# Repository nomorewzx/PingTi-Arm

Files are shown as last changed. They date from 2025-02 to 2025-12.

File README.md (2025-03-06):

# PingTi Arm - A Low-Cost Robotic Arm with Human Arm Length 🤖💪

<center> <a href=./docs/README_CN.md> 中文版 </a> </center>

## What is PingTi Arm? 🤔

**PingTi Arm** is an open-source robotic arm designed based on the [SO-100 arm](https://github.com/TheRobotStudio/SO-ARM100) and is compatible with [Lerobot](https://github.com/huggingface/lerobot). The name "PingTi" comes from the Chinese pinyin "平替" (píng tì), which means "affordable substitute"

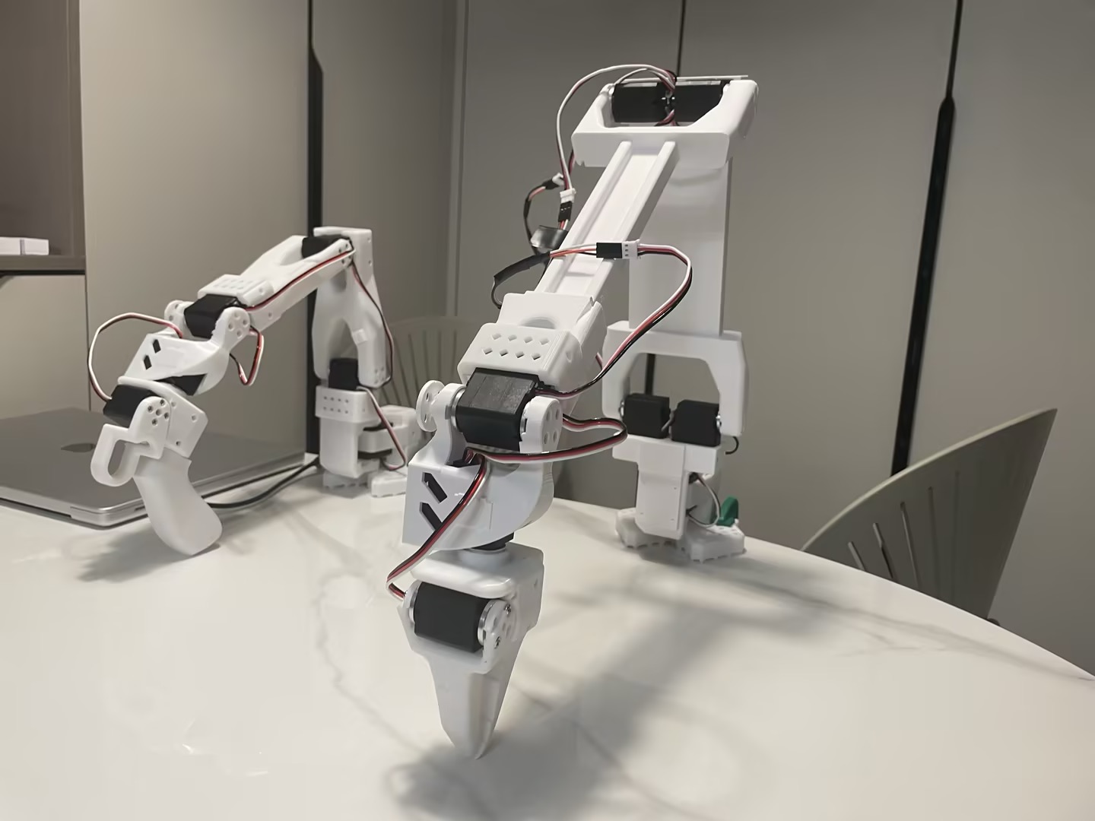
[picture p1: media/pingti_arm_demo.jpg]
PingTi Arm


## Features 
- **Human arm scale**: 600mm arm span (excluding the end effector).
- **Reasonable payload**: Supports up to 500g at maximum arm span.
- **Support setting up Leader-Follower arms** you can setup a pair of Leader-Follower arm using PingTi Arm as follower arm and SO-100 as leader arm
- **Compatible with Lerobot**, You can run teleoperation, data collection and other tasks that Lerobot supports via [pingti_lerobot_bridge](https://github.com/nomorewzx/pingti_lerobot_bridge) sdk
- **Cost Effective**: 
  - A single PingTi arm costs ~ USD 261, 
  - A Lead-Follower setup costs ~ USD 390.
  - If you already own an SO-100 follower arm (12V, 30kg.cm servos), you only need 2 additional servos and a USB drive board (~$157) to assemble the PingTi arm.

## Docs
- [Bills of Materials List](./docs/BOM_List.md) ｜ [Bills of Materials List 中文版](./docs/BOM_List_CN.md)
- [3D Printing](./docs/3d_print.md)
- [Assembly tutorial](./docs/Assembe_tutorial.md)
- [Example of run teleoperation and other tasks via `pingti_lerobot_bridge`](https://github.com/nomorewzx/pingti_lerobot_bridge)
- **(TODO)**: PingTi Arm on [LeKiwi base](https://github.com/SIGRobotics-UIUC/LeKiwi)
- **(TODO)**: [URDF for Simulation](./docs/URDF_SIM.md)

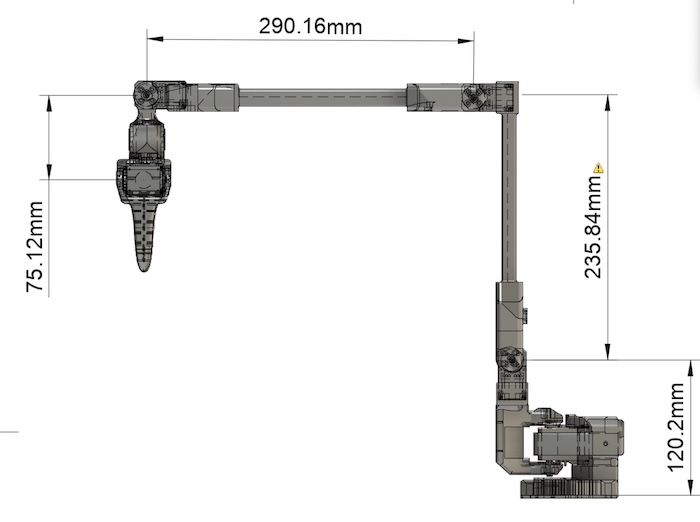
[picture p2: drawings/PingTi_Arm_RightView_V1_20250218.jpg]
The Right View of PingTi Arm


## Recommendation for Beginners

- I strongly recommend you to start with [SO-100](https://github.com/TheRobotStudio/SO-ARM100) and come to PingTi Arm if you are interested in:
    - a longer arm
    - reasonable payload capacity

- As stated before, if you assemble SO-100 with the `12V 30KG.cm` servos, you only need buy 2 more servos and 1 more USB control board to onboard PingTi arm. There is no waste of money

## Caution⚠️
- Avoid sudden movement and stop with heavy payload (e.g. 500g)
- Risk of shoulder joint damage if these conditions are not considered.
- Consider to increase the **infill density** when print the links if you would like to frequently use with heavy payloads

## Acknowledgement

- [SO-100](https://github.com/TheRobotStudio/SO-ARM100)
- [Lerobot](https://github.com/huggingface/lerobot)
- [LeKiwi](https://github.com/SIGRobotics-UIUC/LeKiwi)

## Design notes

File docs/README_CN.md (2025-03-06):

# PingTi Arm - A Low-Cost Robotic Arm with Human Arm Length 🤖💪

## 什么是 PingTi Arm？🤔
PingTi 机械臂基于 [SO-100 机械臂](https://github.com/TheRobotStudio/SO-ARM100) 设计，并与 [Lerobot](https://github.com/huggingface/lerobot) 兼容。PingTi, 即“平替”的拼音。

PingTi Arm

## Features
- **人类臂长尺寸**：臂展为 660mm（不包括末端执行器）。
- **合理的负载能力**：在最大臂展下支持高达 550g 的负载。
- **支持设置主从臂**: 你可以使用SO-100 作为主臂，PingTi Arm作为从臂
- **Lerobot 兼容**: 你可以通过使用 [pingti_lerobot_bridge](https://github.com/nomorewzx/pingti_lerobot_bridge)` sdk 运行遥操作, 数据收集等任务
- **低成本**：
    - 单个 PingTi 机械臂的成本约为 **1800元人民币**，
    - 一对主从臂的组装成本为 **2486元人民币**。
    - 如果你已经组装了一只 SO-100 从动臂(使用12V, 30kg.cm舵机)，那么你只需要再买2个舵机，一个USB驱动板 (973元)，就可以组装 PingTi Arm

## Docs
- [物料清单(淘宝链接版)](./BOM_List_CN.md)
- [3D打印](./3d_print.md)
- [组装教程](./Assemble_tutorial_CN.md)
- 运行遥操作
- [用于仿真的 URDF 文件](./docs/URDF_SIM.md)

PingTi 机械臂的右侧视图

## 初学者推荐

- 强烈建议初学者从 [SO-100](https://github.com/TheRobotStudio/SO-ARM100) 开始，如果对以下内容感兴趣，可以过渡到 PingTi 机械臂：
    - 更长的机械臂
    - 合理的负载能力

- 如前所述，如果您使用 `12V 30KG.cm` 舵机组装 SO-100，只需再购买 2 个舵机和 1 个 USB 控制板即可过渡到 PingTi 机械臂。不会有任何资金浪费。

## 注意事项⚠️
- 避免重负载（例如 600g）情况下进行突然运动和停止。
- 如果不注意这些条件，可能会导致肩关节损坏。
- 如果计划频繁使用重负载，建议在打印机械臂连接件时增加**填充密度**。

## 致谢

- [SO-100](https://github.com/TheRobotStudio/SO-ARM100)
- [Lerobot](https://github.com/huggingface/lerobot)
- [LeKiwi](https://github.com/SIGRobotics-UIUC/LeKiwi)

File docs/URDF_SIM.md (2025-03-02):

### URDF

A PyBullet URDF is created by using [Fusion2PyBullet](https://github.com/yanshil/Fusion2PyBullet/tree/master) , see `./urdf/PingTi_Arm_pybullet/`

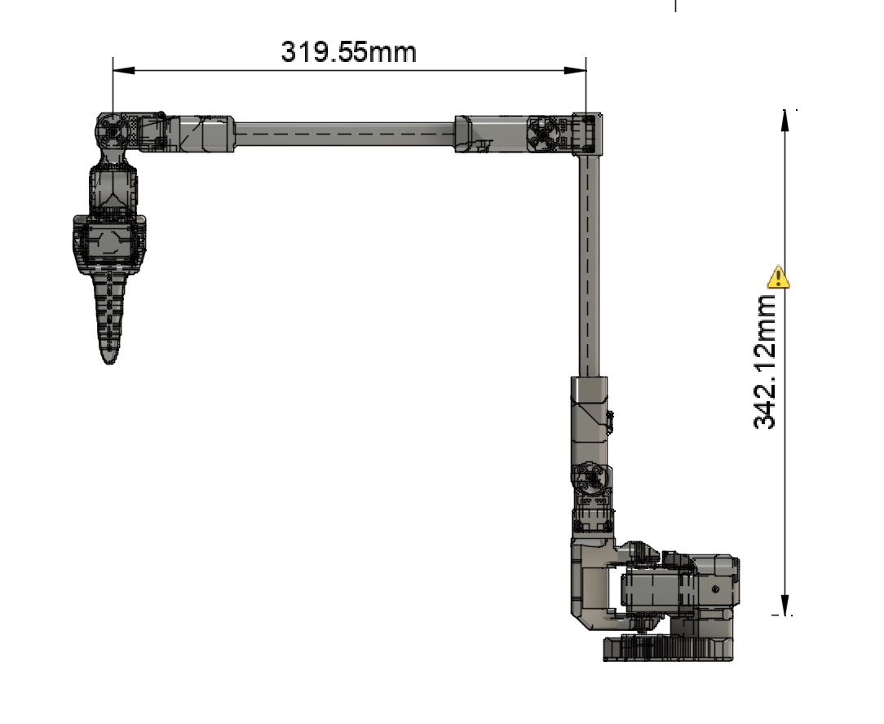
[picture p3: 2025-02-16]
drawings/PingTi_Arm_RightView_V1_20250216.jpg

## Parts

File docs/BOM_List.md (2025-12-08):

## Sourcing Parts

**Note:** The PingTi arm can be used as a follower arm in teleoperation tasks, while the SO-100 arm can serve as the leader arm.

This section includes the Bill of Materials (BOM) for a single PingTi arm and a single SO-100 leader arm. The provided links are for purchasing parts in the U.S. and E.U. For links to purchase parts in China, please refer to the [BOM List 中文版](./BOM_List_CN.md).

#### Parts For PingTi Arm:
| Part | Amount | Unit Cost (US) | Buy US | Unit Cost (EU) | Buy EU |
|---|---|---|---|---|---|
| STS3250 Servo | 2 | $73.89 | [Alibaba](https://www.alibaba.com/product-detail/ST3250-Metal-Serial-Servo-360-Degree_1601383687169.html) | 59.25€ | [Alibaba](https://www.alibaba.com/product-detail/ST3250-Metal-Serial-Servo-360-Degree_1601383687169.html) |
| STS3215 Servo (12V,30 kg.cm) | 6 | $13.89 | [Alibaba](https://www.alibaba.com/product-detail/Feetech-STS3215-SO-100-Servo-12V_1601292634404.html) | 13.00€ | [Alibaba](https://www.alibaba.com/product-detail/Feetech-STS3215-SO-100-Servo-12V_1601292634404.html) |
| Motor Control Board | 1 | $7.05 | [Amazon](https://www.alibaba.com/product-detail/Feetech-FE-URT-1-Multi-Function_1600157148551.html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)| 6.79€ | [Alibaba](https://www.alibaba.com/product-detail/Feetech-FE-URT-1-Multi-Function_1600157148551.html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) |
| Table Clamp 2pcs | 1 | $9.00 | [Amazon](https://www.amazon.com/Mr-Pen-Carpenter-Clamp-6inch/dp/B092L925J4/) | 8.00€ | [Amazon](https://www.amazon.fr/-/en/dp/B08HZ1QRBF/) |
| Dupont Wire | 1 | $6.98 | [Amazon](https://www.amazon.com/Elegoo-EL-CP-004-Multicolored-Breadboard-arduino/dp/B01EV70C78/ref=sr_1_1)| 6.99€ | [Amazon](https://www.amazon.fr/-/en/dp/B01BKN8UX4/ref=sr_1_3) |
| Total | | $261.09 | --- | 218.28€ | --- |

> **Note:** 
> 1. The prices listed above are for reference only; actual prices may vary due to market fluctuations.
> 2. Links for components other than servo motors and USB driver boards are provided for reference only; you may purchase equivalent products with the same specifications from other vendors.
> 3. The Waveshare USB Drive board previously recommended by the SO-100 team was tested and found unable to drive all eight servos of the PingTi Arm. Therefore, the Feetech USB Drive board is used instead. 
> 4. If you are modifying an SO-ARM101 kit that comes with a [Seeed Studio XIAO servo driver board](https://www.alibaba.com/product-detail/105990190-Bus-Servo-Driver-Board-for_1601428837475.html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), you don't have to buy the additional motor board, those are also capable of driving a PingTi Arm.

#### Parts for SO100 Leader Arm:

Note: This BOM list is copied from [SO-100 repo](https://github.com/TheRobotStudio/SO-ARM100)

| Part | Amount | Unit Cost (US) | Buy US | Unit Cost (EU) | Buy EU |
|---|---|---|---|---|---|
| STS3215 Servo (7.V, 20kg.cm)</sup> | 6 | $14 | [Alibaba](https://www.alibaba.com/product-detail/_1601053797763.html) | 13€ | [Alibaba](https://www.alibaba.com/product-detail/_1601053797763.html) |
| Motor Control Board | 1 | $11 | [Amazon](https://www.amazon.com/Waveshare-Integrates-Control-Circuit-Supports/dp/B0CTMM4LWK/) | 12€ | [Amazon](https://www.amazon.fr/-/en/dp/B0CJ6TP3TP/)|
| USB-C Cable 2 pcs | 1 | $7 | [Amazon](https://www.amazon.com/Charging-etguuds-Charger-Braided-Compatible/dp/B0B8NWLLW2/?th=1) | 7€ | [Amazon](https://www.amazon.fr/dp/B07BNF842T/) |
| Power Supply</sup> | 1 | $10 | [Amazon](https://www.amazon.com/Facmogu-Switching-Transformer-Compatible-5-5x2-1mm/dp/B087LY41PV/) | 13€ | [Amazon](https://www.amazon.fr/-/en/dp/B01HRR9GY4/) |
| Table Clamp 2pcs | 1 | $9 | [Amazon](https://www.amazon.com/Mr-Pen-Carpenter-Clamp-6inch/dp/B092L925J4/) | 8€ | [Amazon](https://www.amazon.fr/-/en/dp/B08HZ1QRBF/)|
| Screwdriver Set<sup>[3](#myfootnote3)</sup> | 1 | $6 | [Amazon](https://www.amazon.com/Precision-Phillips-Screwdriver-Electronics-Computer/dp/B0DB227RTH) | 10€ | [Amazon](https://www.amazon.fr/dp/B08ZXVMVYD/) |
| Total |---| $127 |---| 128€ |---|

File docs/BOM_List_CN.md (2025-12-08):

## Sourcing Parts

在遥操作方案中。 PingTi 机械臂可以作为遥操作任务中的从动臂, S0-100 机械臂可以作为主动臂。BOM List 分别列出了PingTi机械臂和SO100 主动臂的零部件以及购买链接

#### PingTi Arm:
| Part | Amount | Unit Cost (RMB) | Links |
|---|---|---|--|
| STS3250 Servo (12V, 50kg.cm) | 2 | 464.00 | [淘宝链接](https://item.taobao.com/item.htm?id=764814801381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) |
| STS3215 Servo (12V, 30kg.cm) | 6 | 115.00 | [淘宝链接](https://item.taobao.com/item.htm?id=712179366565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) |
| 总线舵机驱动板 | 1 | 45.00 | [淘宝链接](https://item.taobao.com/item.htm?id=575365901461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) |
| 电源 (12V5A) | 1 | 35.00 | [淘宝链接](https://detail.tmall.com/item.htm?id=716728018390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) |
| 桌面夹(2支) | 1 | 19.50 | [淘宝链接](https://detail.tmall.com/item.htm?id=799008477371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) |
| 杜邦线 Dupont Wire  | 1 | 2.35 | [淘宝链接](https://detail.tmall.com/item.htm?id=41254478179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) |
| Total  | --- | 1,719.1 | --- |

#### SO100 主动臂:
| Part | Amount | Unit Cost (RMB) | Links |
|---|---|---|-----|
| STS3215 Servo (7.4V, 19kg.cm) | 6 | 99.00 | [淘宝链接](https://item.taobao.com/item.htm?id=712179366565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) |
| 舵机总线控制板 | 1 | 24.00 | [淘宝链接](https://item.taobao.com/item.htm?id=738955630278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) |
| USB TypeC 连接线 | 1 | 22.00 | [淘宝链接](https://detail.tmall.com/item.htm?id=527849163284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) |
| 电源 (7.4V, 2A) | 1 | 13.80 | [淘宝链接](https://item.taobao.com/item.htm?id=821893750669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) |
| 桌面夹(2支) | 1 | 19.50 | [淘宝链接](https://detail.tmall.com/item.htm?id=799008477371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) |
| 螺丝刀套装 | 1 | 19.90 | [淘宝链接](https://detail.tmall.com/item.htm?id=586737442458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) |
| **Total** | | **691.9** | **---** |

> **Note:** 
>1. 以上价格为参考价格，实际价格可能因市场波动而有所变化。
>2. 除舵机外和USB驱动板外，其余零部件的链接只是参考，你可以购买其它商家的相同规格的产品
>3. SO-100 之前推荐的 Waveshare USB Drive board 经测试无法驱动PingTi Arm的8个舵机，因此使用Feetech 的 USB Drive board
> 4. 如果您改装的是自带 [Seeed Studio XIAO 舵机驱动板](https://www.alibaba.com/product-detail/105990190-Bus-Servo-Driver-Board-for_1601428837475.html) 的 SO-ARM101 套件，则无需额外购买电机驱动板，该驱动板同样能够驱动整套 PingTi 机械臂。

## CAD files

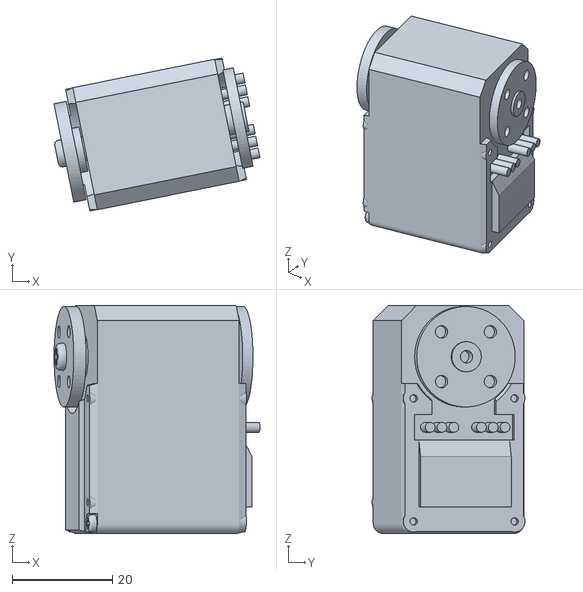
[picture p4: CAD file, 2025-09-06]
Simulation/PingTi_Arm_v3/urdf/meshes/STS3215_shoulder_pitch_2_1.stl
41.0 x 30.5 x 45.4

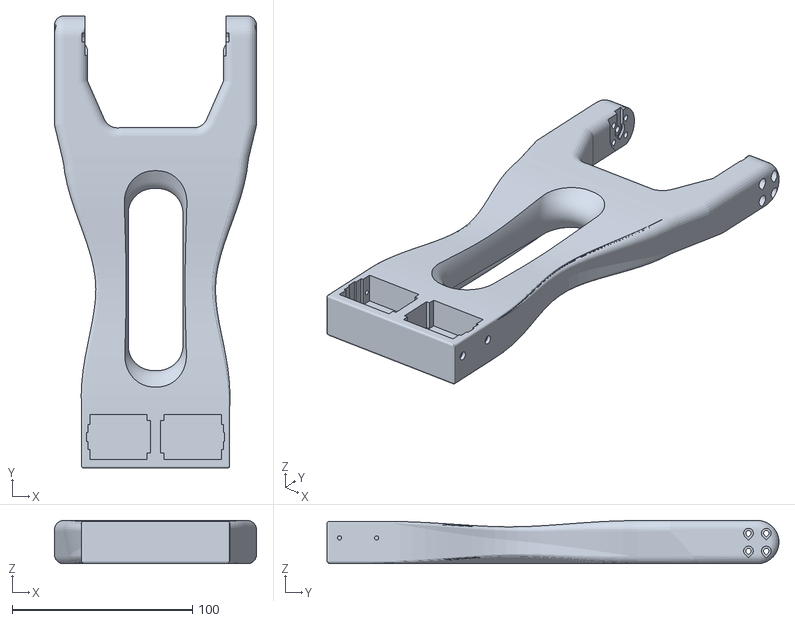
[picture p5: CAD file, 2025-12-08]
stl_3d_printing/shoulder_link_alternate.stl
112.1 x 250.8 x 23.9

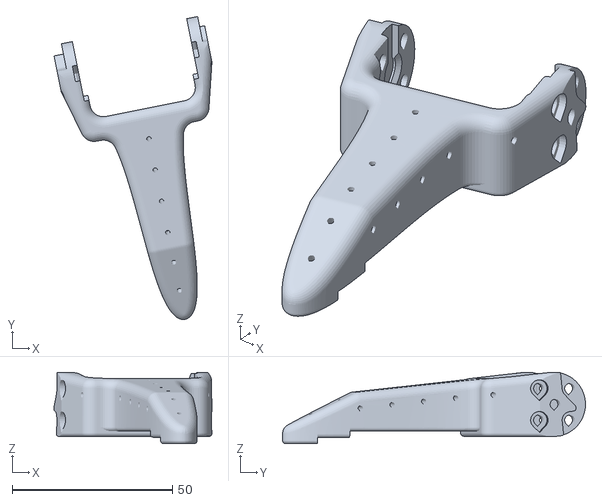
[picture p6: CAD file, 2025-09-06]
Simulation/PingTi_Arm_v3/urdf/meshes/moving_gripper_1.stl
49.3 x 94.7 x 22.3

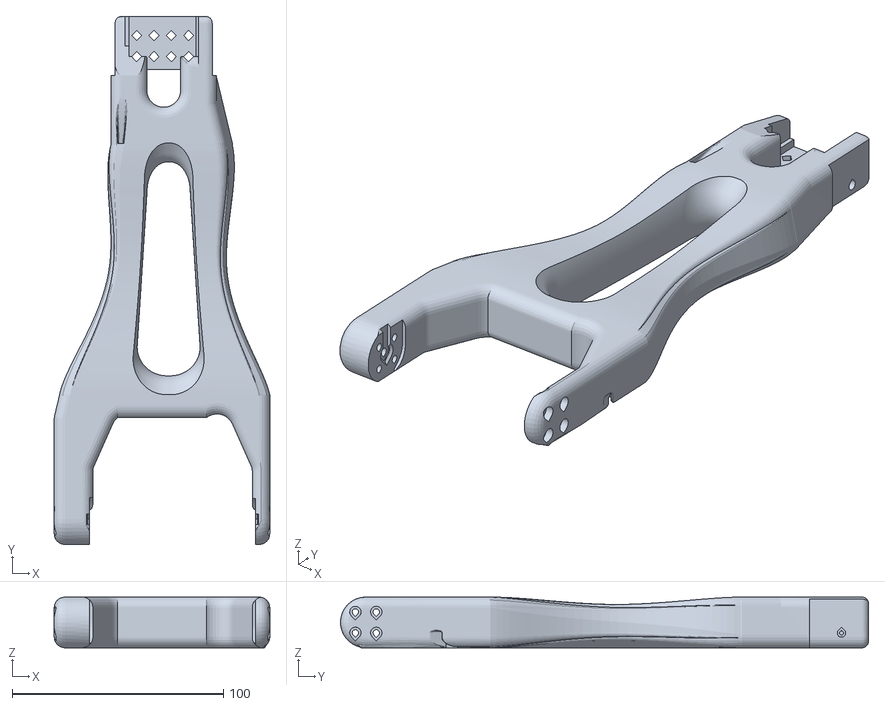
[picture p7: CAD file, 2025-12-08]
stl_3d_printing/elbow_link_alternate.stl
102.1 x 250.2 x 24.1

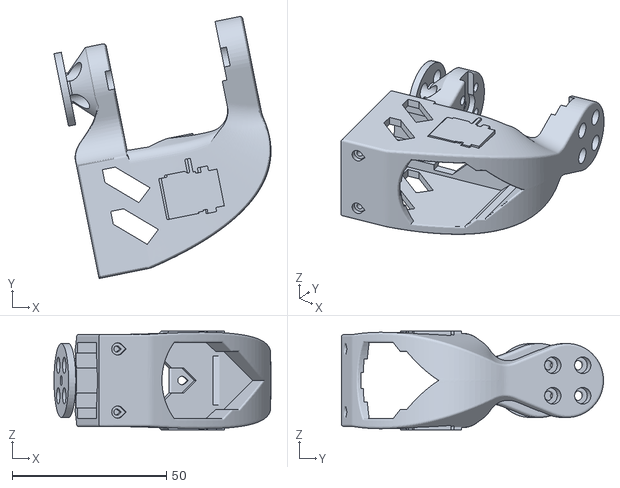
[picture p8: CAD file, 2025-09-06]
Simulation/PingTi_Arm_v3/urdf/meshes/wrist_link_1.stl
70.4 x 85.0 x 32.0

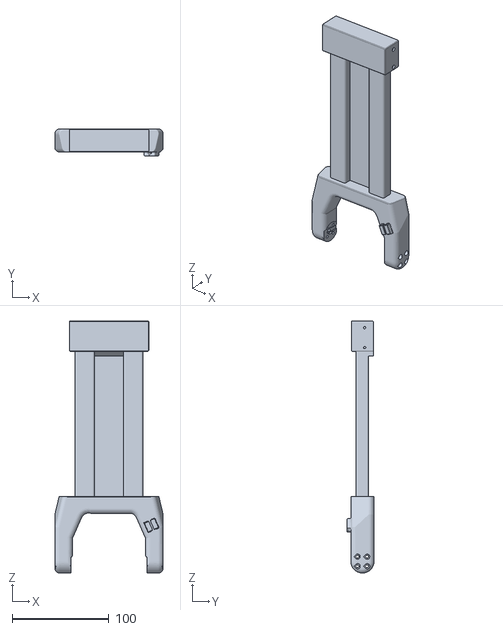
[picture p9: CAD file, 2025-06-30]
stl_3d_printing/shoulder_link.stl
112.1 x 28.0 x 260.8

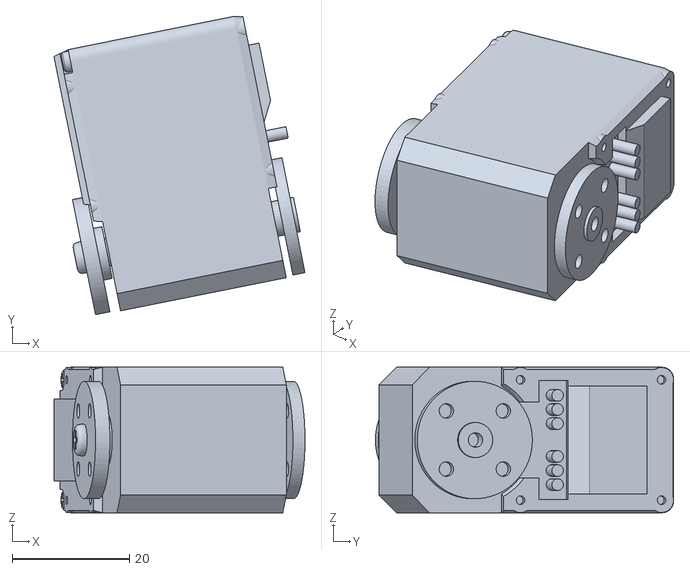
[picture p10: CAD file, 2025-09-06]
Simulation/PingTi_Arm_v3/urdf/meshes/STS3215_wrist_pitch_1.stl
42.8 x 50.8 x 24.8

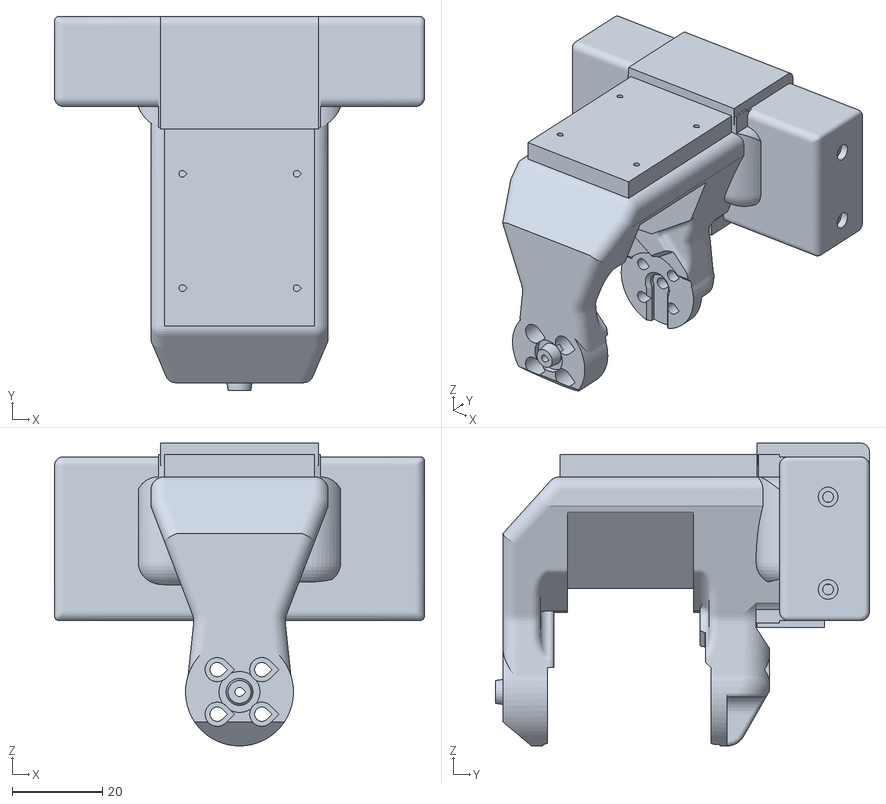
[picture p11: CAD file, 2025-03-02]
stl_3d_printing/base_yaw_link.stl
82.2 x 83.1 x 67.3

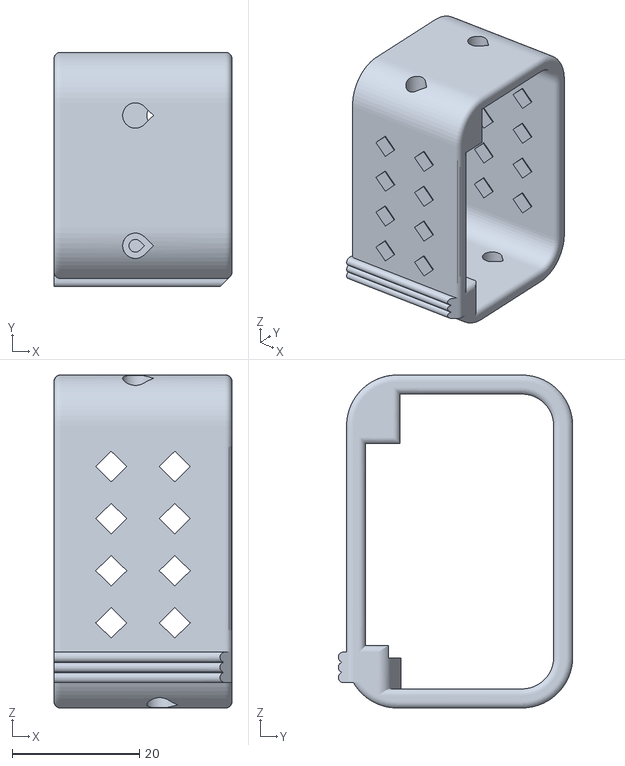
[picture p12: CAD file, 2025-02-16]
stl_3d_printing/wrist_servo_mount_frame_from_so100.stl
28.0 x 36.9 x 52.4

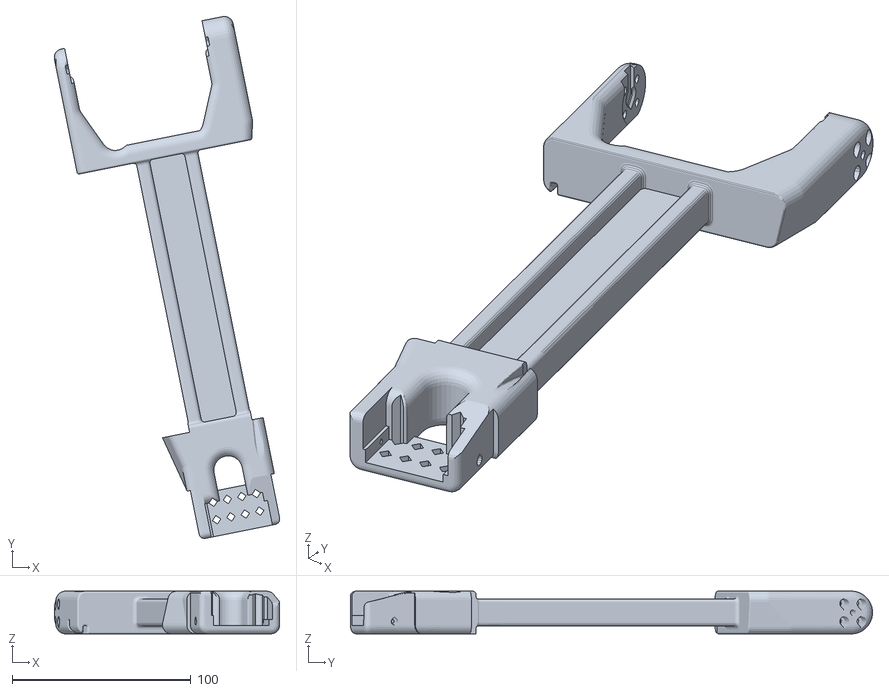
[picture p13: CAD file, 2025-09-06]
Simulation/PingTi_Arm_v3/urdf/meshes/elbow_link_1.stl
126.3 x 292.4 x 24.0

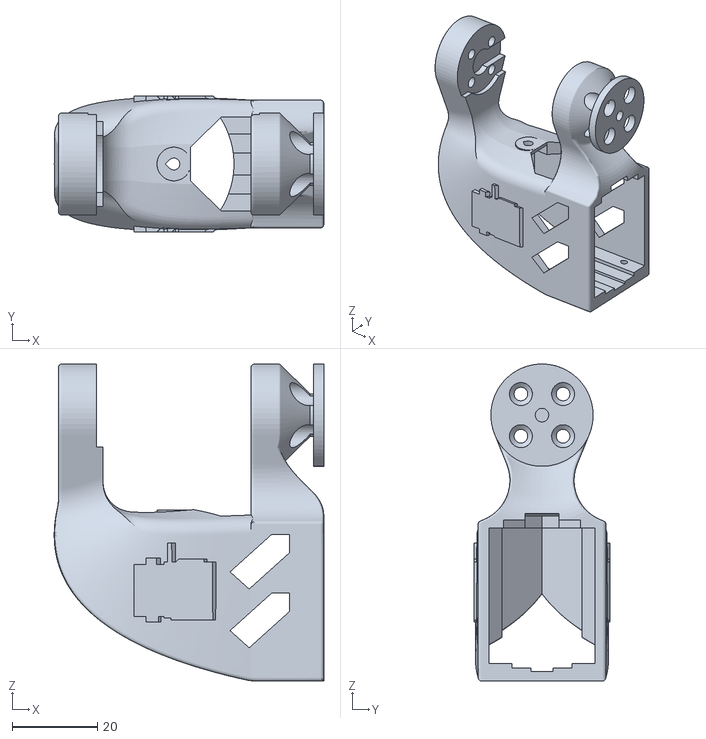
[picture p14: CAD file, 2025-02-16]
stl_3d_printing/wrist_pitch_link_from_so100.stl
63.3 x 32.0 x 74.4

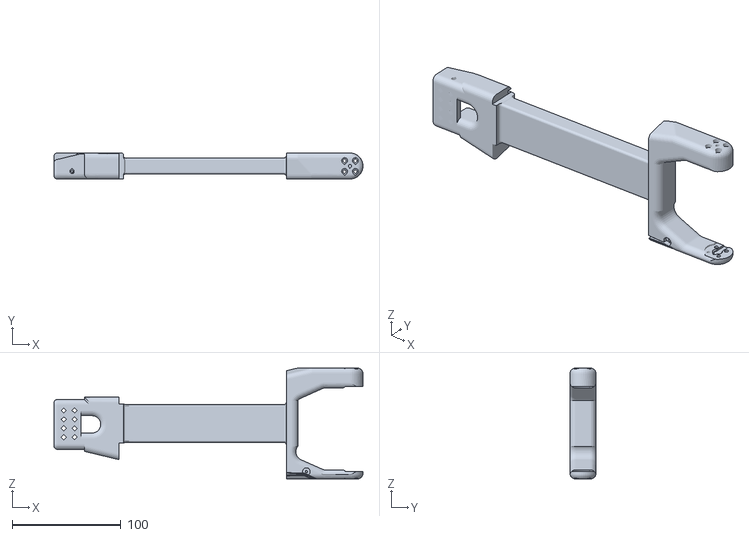
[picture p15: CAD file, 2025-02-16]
stl_3d_printing/elbow_link.stl
284.7 x 24.0 x 102.1

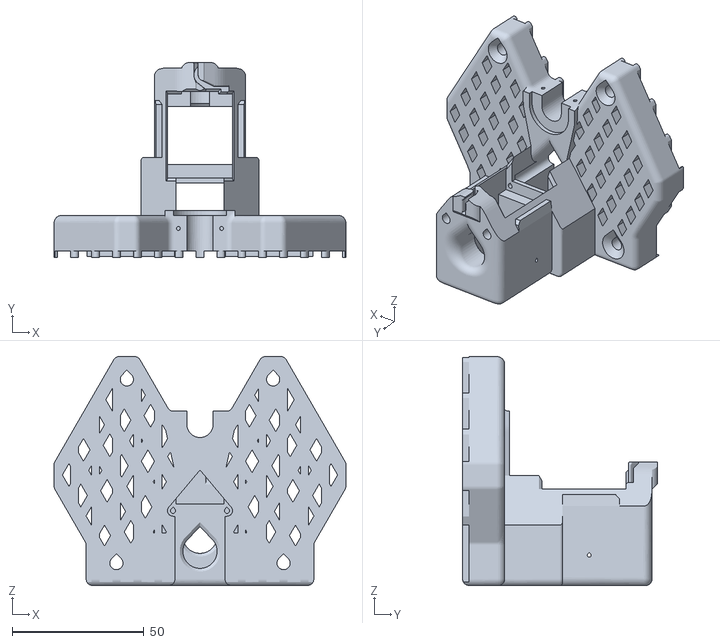
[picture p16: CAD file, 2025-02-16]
stl_3d_printing/base_link_from_so100.stl
110.9 x 74.0 x 87.0

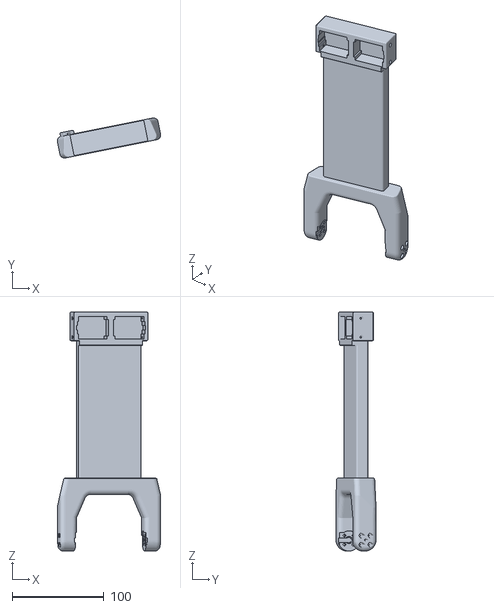
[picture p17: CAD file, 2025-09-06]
Simulation/PingTi_Arm_v3/urdf/meshes/shoulder_link_1.stl
112.9 x 43.8 x 260.8

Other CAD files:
Simulation/PingTi_Arm_v3/urdf/meshes/STS3215_wrist_roll_1.stl
Simulation/PingTi_Arm_v3/urdf/meshes/STS3215_shoulder_pitch_1_1.stl
Simulation/PingTi_Arm_v3/urdf/meshes/STS3215_elbow_pitch_2_1.stl
stl_3d_printing/base_link_servo_mount_frame_from_so100.stl
Simulation/PingTi_Arm_v3/urdf/meshes/STS3215_base_yaw_1.stl
Simulation/PingTi_Arm_v3/urdf/meshes/STS3215_elbow_pitch_1_1.stl
Simulation/PingTi_Arm_v3/urdf/meshes/STS3215_gripper_1.stl
Simulation/PingTi_Arm_v3/urdf/meshes/base_link.stl
Simulation/PingTi_Arm_v3/urdf/meshes/base_yaw_link_1.stl
Simulation/PingTi_Arm_v3/urdf/meshes/gripper_mount_1.stl
Simulation/PingTi_Arm_v3/urdf/meshes/wrist_mount_link_1.stl
fusion/PingTi_Arm_5DOF_v4.f3d
stl_3d_printing/base_link_idle_clamp_from_so100.stl
stl_3d_printing/moving_gripper_from_so100.stl
stl_3d_printing/wrist_roll_from_so100.stl

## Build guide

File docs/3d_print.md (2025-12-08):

# 3D Printing

### PingTi arm
> Estimated time: ~20 hours

You can find STL files for the 3D-printed parts in dir `../stl_3d_printing/`. I printed the parts on [Bambu Lab A1 Printer](https://www.amazon.com/Multi-Color-Precision-Full-Auto-Calibration-Compensation/dp/B0D17V4SKM?th=1) using [Bambu Lab PETG](https://www.matterhackers.com/store/l/bambu-lab-petg-basic-filament-175mm-1kg/sk/MW6ED56H) filament

The printer settings are:
- Layer height: 0.2mm
- Initial layer height: 0.2mm
- Sparse infill density: 13%
- Enable support

There are also two additional parts for the main extension links, elbow_link_alternate and shoulder_link_alternate which can be used instead of the usual elbow and shoulder links. They are a slightly shortened so they can be printed horizontally on a Bambu A1 print bed and mimic the SO-ARM101 design.

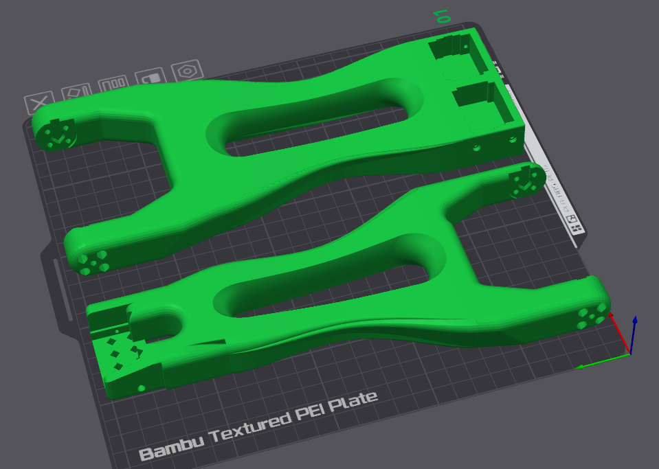
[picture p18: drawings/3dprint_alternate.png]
extra links


**Note**: The STL files with suffix `_from_so100` means I copy these files directly from [SO-100 repo](https://github.com/TheRobotStudio/SO-ARM100)

### SO-100 Leader Arm
You can find the STL files from official github repo [SO-100 Leader Arm](https://github.com/TheRobotStudio/SO-ARM100/blob/main/stl_files_for_3dprinting/Leader/Print_Leader_SO_ARM100_08k_Ender.STL)

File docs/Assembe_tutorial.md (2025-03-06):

## Placement of Servos

There are 8 servos, including 2 * ST-3250 (50kg.cm) servos and 6 * ST-3215 (30kg.cm) servos, and the placement of servos can be found below:

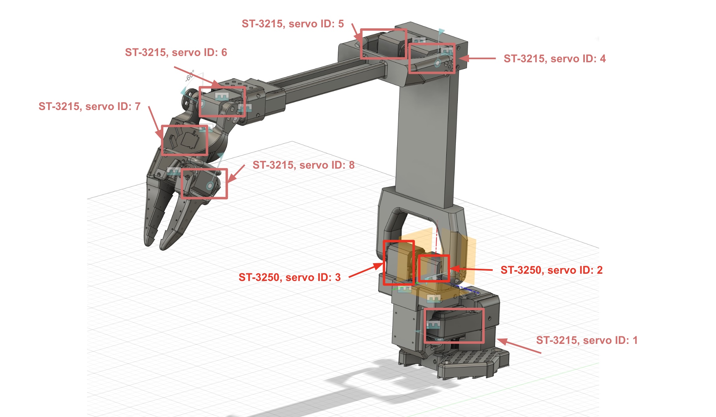
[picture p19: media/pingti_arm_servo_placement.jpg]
Placement of servos


## Placement of Links

There are 10 links and the placement for different links can be found below:

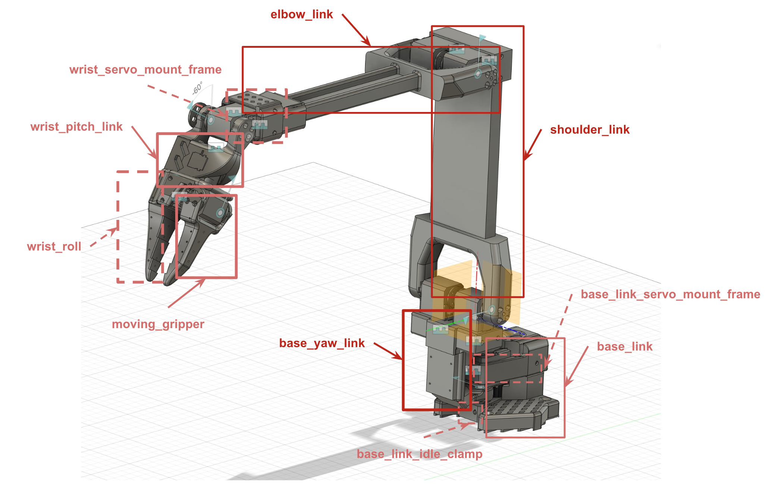
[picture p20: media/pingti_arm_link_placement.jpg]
Placement of links


## USB board connection
Connect the power supply and servos by referring image blow.

> **Note**: The `V1` port is labeled as `DC6V-9V`, but I checked with Feetech tech support and confirmed that a 12V power supply can be safely connected

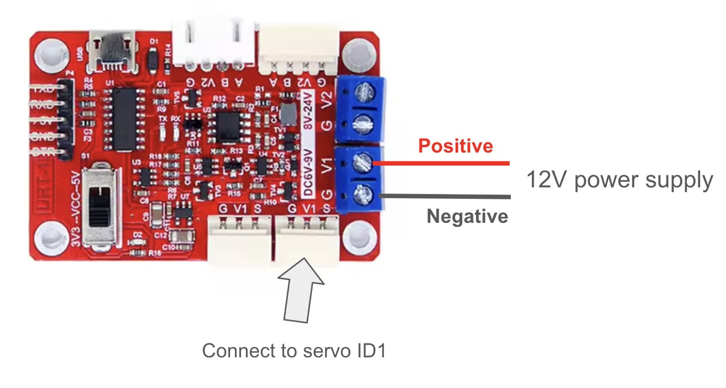
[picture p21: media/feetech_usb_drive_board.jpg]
Feetech USB Drive Board


## Configure Servos using LeRobot

### A. Install LeRobot library and Find USB port

Refer the **Install LeRobot** section of offical [LeRobot tutorial](https://github.com/huggingface/lerobot/blob/main/examples/10_use_so100.md#b-install-lerobot) 

You should also find the USB port by following instructions of **Find the USB ports associated to each arm** in [LeRobot tutorial](https://github.com/huggingface/lerobot/blob/main/examples/10_use_so100.md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)

>**Note**: The port number of the Feetech USB board may occasionally change. If you encounter a "port not found" error after identifying the port earlier, please recheck the USB port.

### B. Configure the servos using LeRobot

Below script demos how to configure servo. The configuration script will do 2 things:
1. Set the servo's id as `1`
2. Set the position of the servo to `2048`

```bash
python lerobot/scripts/configure_motor.py \
  --port /dev/tty.usbmodem58760432961 \
  --brand feetech \
  --model sts3215 \
  --baudrate 1000000 \
  --ID 1
```

Then unplug your servo and plug the second servo (it should be a ST3250 servo) and set its ID to 2. **Here you can keep using the `--model sts3215` since both model types shares the same SDK and control table.**

```bash
python lerobot/scripts/configure_motor.py \
  --port /dev/tty.usbmodem58760432961 \
  --brand feetech \
  --model sts3215 \
  --baudrate 1000000 \
  --ID 2
```

Redo the process for all your motors until ID 8. Please note that the IDs for 2 ST-3250 servos should be **2** and **3**. You can also see servo placement drawing above for reference.

### C. Add motor horn to all 8 servos
You can refer to LeRobot official video for adding the motor horn to all 8 servos. The video can be found here [Add Motor Horn to servos](https://www.youtube.com/watch?v=FioA2oeFZ5I&list=PLo2EIpI_JMQu5zrDHe4NchRyumF2ynaUN&index=8&t=570s) 

## Assemble of PingTi Aarm

### Assemble of Base
See SO-100 assemble video for the assembly of base links with servo (ID 1). Specifically, you should look at the **Step4.1 to Step4.4** in [this video](https://www.youtube.com/watch?v=FioA2oeFZ5I&list=PLo2EIpI_JMQu5zrDHe4NchRyumF2ynaUN&index=9&t=610s)

### Assemble of Shoulder
**Connecting wires to servos** The shoulder joint consists of 2 `ST-3250` servos and you should connect all 4 wires before putting the servos into slots, see image below. 
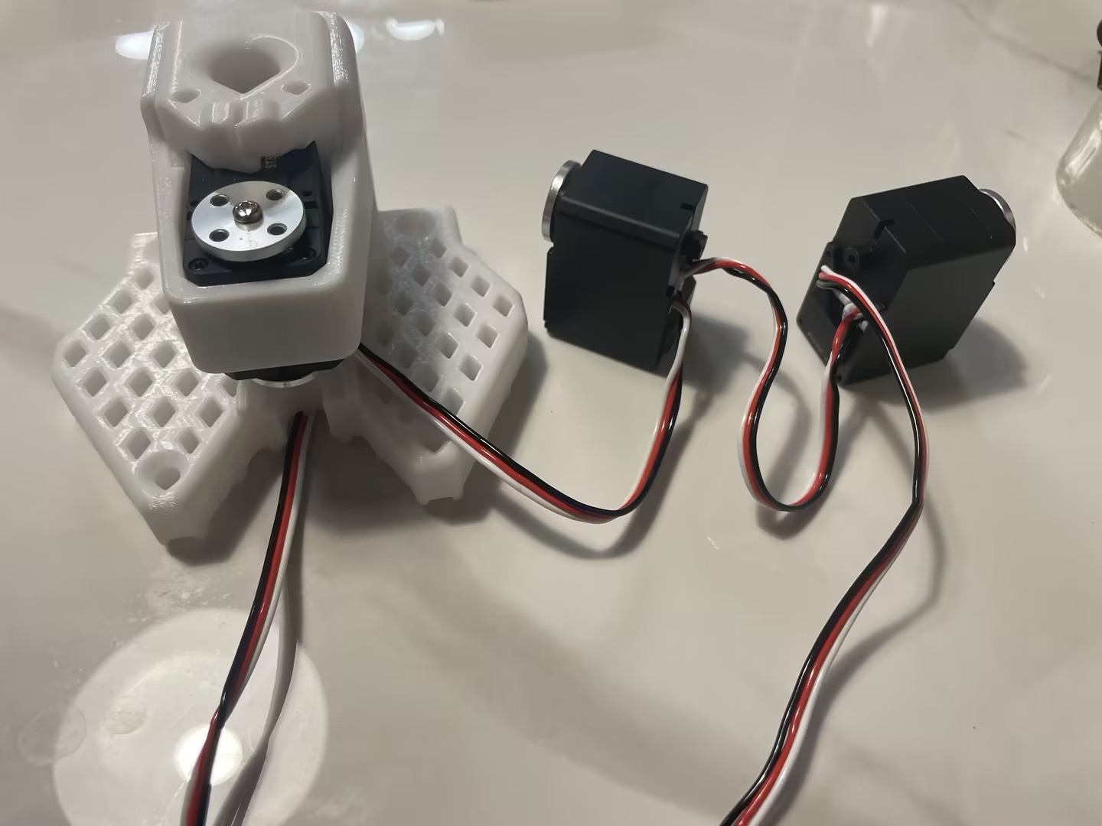
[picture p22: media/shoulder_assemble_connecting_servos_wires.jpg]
wires connection


**Putting servos into slots of base_yaw_link** Put the `ID 2` servo on the left slot and `ID 3` servo on the right slot. Secure the servo with four M2x5 screws. See image below
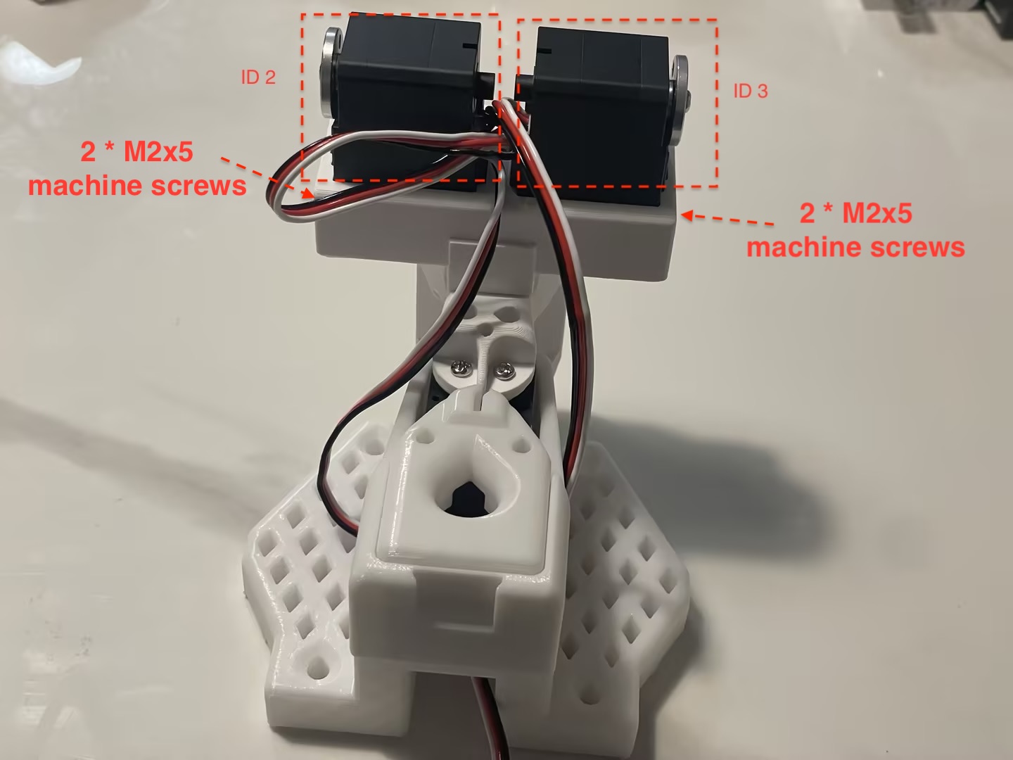
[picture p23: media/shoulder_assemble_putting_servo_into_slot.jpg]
putting servos into slot


**Attaching shoulder link to servo horns** Use 8 M3x6 machine screws to attach shoulder link to servo horns. Pls note the shoulder link should be vertically attached to the servo horns and servo horns on its end should face forward. See image below.

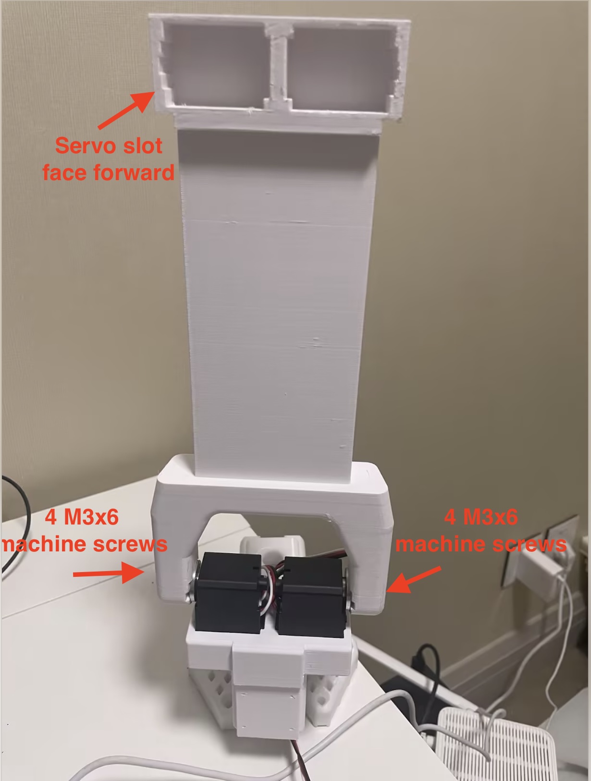
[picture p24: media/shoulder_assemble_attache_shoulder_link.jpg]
attach shoulder link


### Assemble of Elbow
**Connecting wires to servos** The elbow joint consits of 2 `ST-3215` servos with `ID 4` and `ID 5`. You should connect wires properly before putting servos into slot. See image below

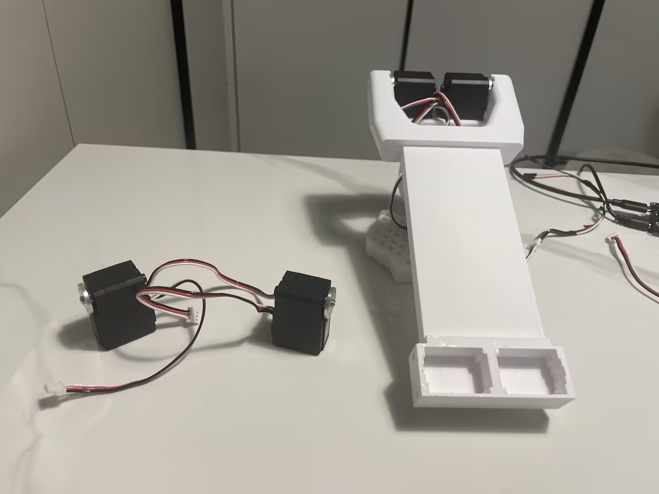
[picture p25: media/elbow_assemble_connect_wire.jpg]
connect wires


**Putting servos into slots and attache elbow link** Put the `ID4` and `ID5` into servo slots like image below and secure the servos using four M2x5 screws. Also attach the elbow link to servo horns using 8 M3x6 machine screws. 

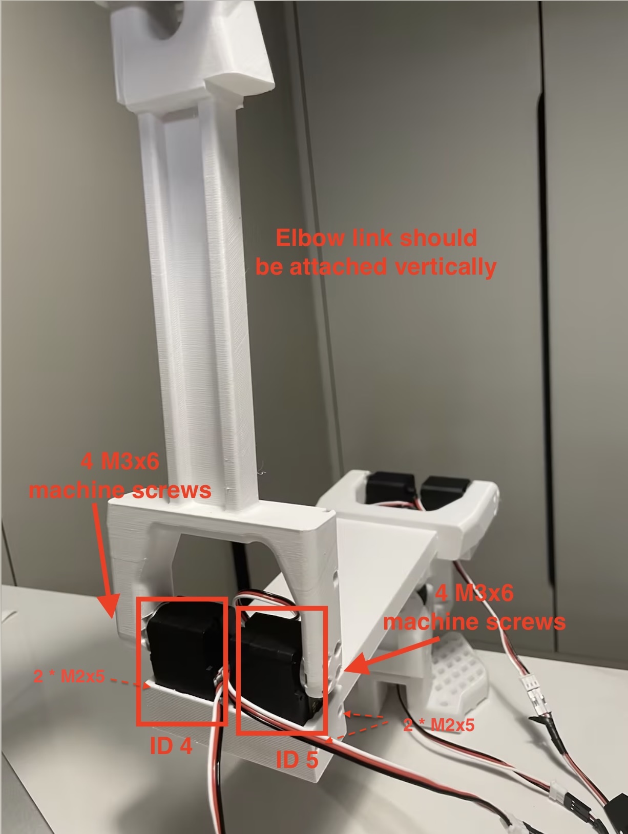
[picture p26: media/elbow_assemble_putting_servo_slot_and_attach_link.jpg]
putting servo and attach links


### Assemble of Wrist and Gripper
See SO-100 assemble video for the assembly of wrist links, gripper links and servos (you would use servos with id 6, 7 and 8). 

Specifically, you should start from **Step 4.9 to Step 4.12** in [this video](https://www.youtube.com/watch?v=FioA2oeFZ5I&list=PLo2EIpI_JMQu5zrDHe4NchRyumF2ynaUN&index=11&t=669s)

## Assemble of SO-100 Leader Arm
See the [SO-100 assemble video for Leader Arm](https://www.youtube.com/watch?v=FioA2oeFZ5I&list=PLo2EIpI_JMQu5zrDHe4NchRyumF2ynaUN&index=12&t=707s)

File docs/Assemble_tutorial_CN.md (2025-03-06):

## 舵机放置

PingTi arm 共有8个舵机，包括2个ST-3250（50kg.cm）舵机和6个ST-3215（30kg.cm）舵机，舵机的放置位置如下：

舵机放置

## 连杆放置

PingTi arm 共有10个连杆，不同连杆的放置位置如下：

连杆放置

## USB 板连接

请参考下方图片连接电源和舵机。

> **注意**：`V1` 端口标注为 `DC6V-9V`，但经过咨询 Feetech 技术支持，确认可以安全连接 12V 电源。

Feetech USB 驱动板

## 使用LeRobot配置舵机

### A. 安装LeRobot库并查找USB端口

参考官方[LeRobot教程](https://github.com/huggingface/lerobot/blob/main/examples/10_use_so100.md#b-install-lerobot)中的**安装LeRobot**部分。

您还应按照[LeRobot教程](https://github.com/huggingface/lerobot/blob/main/examples/10_use_so100.md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)中的**查找与每个机械臂关联的USB端口**部分的说明查找USB端口。

### B. 使用LeRobot配置舵机

以下脚本演示了如何配置舵机。配置脚本将执行以下两个任务：
1. 将舵机的ID设置为`1`
2. 将舵机的位置设置为`2048`

```bash
python lerobot/scripts/configure_motor.py \
  --port /dev/tty.usbmodem58760432961 \
  --brand feetech \
  --model sts3215 \
  --baudrate 1000000 \
  --ID 1
```

然后拔下您的舵机并插入第二个舵机（第二个舵机应为`ST-3250`舵机），并将其ID设置为`2`。这里您可以继续使用`--model sts3215` 参数，因为两种型号共享相同的SDK和控制表。

```bash
python lerobot/scripts/configure_motor.py \
  --port /dev/tty.usbmodem58760432961 \
  --brand feetech \
  --model sts3215 \
  --baudrate 1000000 \
  --ID 2
```

重复此过程，直到所有舵机的ID设置为8。请注意，2个ST-3250舵机的ID应为`2`和`3`。您也可以参考上面的舵机放置图。

### C. 为所有8个舵机安装舵盘

您可以参考LeRobot官方视频为所有8个舵机安装舵盘。视频链接如下：[Add Motor Horn to servos](https://www.youtube.com/watch?v=FioA2oeFZ5I&list=PLo2EIpI_JMQu5zrDHe4NchRyumF2ynaUN&index=8&t=570s) 

## PingTi机械臂组装

### Base 组装
参考SO-100组装视频，组装base link 与舵机（ID `1`）。具体来说，您应查看[此视频](https://www.youtube.com/watch?v=FioA2oeFZ5I&list=PLo2EIpI_JMQu5zrDHe4NchRyumF2ynaUN&index=9&t=610s)中的**Step 4.1到Step 4.4**。

### Shoulder 组装
**连接舵机线缆** Shoulder 关节由2个`ST-3250`舵机组成，您应在将舵机放入槽位之前连接所有4根线缆，如下图所示。  
线缆连接

**将舵机放入base_yaw_link的槽位** 将`ID 2`舵机放在左侧槽位，`ID 3`舵机放在右侧槽位。使用4个M2x5螺丝固定舵机。如下图所示  

将舵机放入槽位

**将肩部连杆连接到舵机臂** 使用8个M3x6机器螺钉将 Shoulder link 连接到舵盘。请注意，Shoulder link 应垂直连接到舵盘，且Shoulder link 末端的舵机槽应朝前。如下图所示。

连接肩部连杆

### Elbow 组装
**连接舵机线缆** Elbow 关节由2个`ST-3215`舵机组成，ID分别为`ID 4`和`ID 5`。您应在将舵机放入槽位之前正确连接线缆。如下图所示  

连接线缆

**将 Shoulder link 槽位并连接肘部连杆** 如下图所示，将`ID4`舵机放入左侧槽位，`ID5`舵机放入右侧槽位，使用4个M2x5螺丝固定舵机。同时使用8个M3x6机器螺钉将 Elbow link 连接到舵盘。

放入舵机并连接连杆

### Wrist & Gripper 组装
参考SO-100组装视频，组装腕部连杆、夹爪连杆和舵机（您将使用ID为6、7和8的舵机）。  

具体来说，您应从[此视频](https://www.youtube.com/watch?v=FioA2oeFZ5I&list=PLo2EIpI_JMQu5zrDHe4NchRyumF2ynaUN&index=11&t=669s)中的**步骤4.9到步骤4.12**开始。

## SO-100主控机械臂组装
参考[SO-100主控机械臂组装视频](https://www.youtube.com/watch?v=FioA2oeFZ5I&list=PLo2EIpI_JMQu5zrDHe4NchRyumF2ynaUN&index=12&t=707s)

## Footnote

在 Bilibili 也可以找到 SO-100 相关的组装教程，例如 [30分钟装好SO-100-保姆级视频组装教程-从臂](https://www.bilibili.com/video/BV1CNNoeeEpJ/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)

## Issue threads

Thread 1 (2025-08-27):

PingTing arm URDF import fails

nonotaku, 2025-08-27:
Hi, I’m trying to import the PingTing arm URDF and it errors in Blender (via Phobos). The traceback ends with TypeError: 'NoneType' object is not iterable, which seems to come from a <material> without a <color> or an undefined named material in the URDF. Could you please verify/fix the URDF materials?

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

nomorewzx, 2025-09-06:
Hi, @nonotaku

I updated the URDF for simulation and verify it using URDF viwer extension of VS Code. Pls see `./Simulation/PingTi_Arm_v3/urdf`

May you have a try using Blender?

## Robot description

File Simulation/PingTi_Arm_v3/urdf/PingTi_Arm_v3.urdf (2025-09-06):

<?xml version="1.0" ?>
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
<robot name="PingTi_Arm_v3">
  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
  <link name="base_link">
    <inertial>
      <origin rpy="0 0 0" xyz="-3.2942227991692706e-06 -0.016410113639789673 0.025524321515390098"/>
      <mass value="1.1606702094747876"/>
      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
    </inertial>
    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
  </link>
  <link name="elbow_link_1">
    <inertial>
      <origin rpy="0 0 0" xyz="-0.006368202700747123 -0.13257432066234234 -0.000710253994771759"/>
      <mass value="1.3232321824941673"/>
      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
    </inertial>
    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
  </link>
  <link name="STS3215_wrist_pitch_1">
    <inertial>
      <origin rpy="0 0 0" xyz="-0.015103902665090832 -0.015364326843161913 -2.529961420916216e-07"/>
      <mass value="0.2843033831904074"/>
      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
    </inertial>
    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
  </link>
  <link name="wrist_link_1">
    <inertial>
      <origin rpy="0 0 0" xyz="0.019701433146455137 -0.022957641297722542 -5.135733105687823e-05"/>
      <mass value="0.2392168278135931"/>
      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
    </inertial>
    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
  </link>
  <link name="STS3215_wrist_roll_1">
    <inertial>
      <origin rpy="0 0 0" xyz="-0.008933246759550137 -0.020582128831145963 -2.5299615225016225e-07"/>
      <mass value="0.2843033831904074"/>
      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
    </inertial>
    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
  </link>
  <link name="gripper_mount_1">
    <inertial>
      <origin rpy="0 0 0" xyz="0.0026773059376802855 -0.020173178230651845 -0.01565257096694167"/>
      <mass value="0.44698022927880193"/>
      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
    </inertial>
    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
  </link>
  <link name="STS3215_gripper_1">
    <inertial>
      <origin rpy="0 0 0" xyz="0.00012461197605628804 2.539181574140459e-05 0.02239868354094854"/>
      <mass value="0.2843033831904074"/>
      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
    </inertial>
    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
  </link>
  <link name="moving_gripper_1">
    <inertial>
      <origin rpy="0 0 0" xyz="-0.014635153287696837 -0.03276490039211122 -0.0005006987132448737"/>
      <mass value="0.1586808414280307"/>
      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
    </inertial>
    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
  </link>
  <link name="wrist_mount_link_1">
    <inertial>
      <origin rpy="0 0 0" xyz="0.022710832853232152 0.004489136774674496 0.0018439782253499293"/>
      <mass value="0.10853073755546008"/>
      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
    </inertial>
    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
  </link>
  <link name="STS3215_base_yaw_1">
    <inertial>
      <origin rpy="0 0 0" xyz="6.752884890919568e-12 0.02300097243678148 0.00012706492471613318"/>
      <mass value="0.2843033831904074"/>
      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
    </inertial>
    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
  </link>
  <link name="base_yaw_link_1">
    <inertial>
      <origin rpy="0 0 0" xyz="0.0066121913949635435 -0.03322206721963538 0.03628999238042017"/>
      <mass value="0.8041215139582379"/>
      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
    </inertial>
    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
  </link>
  <link name="STS3215_shoulder_pitch_1_1">
    <inertial>
      <origin rpy="0 0 0" xyz="0.00012478845663918547 2.5028932493509348e-05 0.02239902756319745"/>
      <mass value="0.2843033831904074"/>
      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
    </inertial>
    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
  </link>
  <link name="STS3215_shoulder_pitch_2_1">
    <inertial>
      <origin rpy="0 0 0" xyz="-0.00012502334154068304 -2.491142533807278e-05 0.022399027563196117"/>
      <mass value="0.2843033831904074"/>
      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
    </inertial>
    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
  </link>
  <link name="shoulder_link_1">
    <inertial>
      <origin rpy="0 0 0" xyz="-0.04009132750395989 -0.008071300634675801 0.1143995501318232"/>
      <mass value="1.815312307803877"/>
      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
    </inertial>
    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
  </link>
  <link name="STS3215_elbow_pitch_1_1">
    <inertial>
      <origin rpy="0 0 0" xyz="0.004523009170013775 -0.021937733328752027 -2.5253846619444076e-07"/>
      <mass value="0.2843033831904074"/>
      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
    </inertial>
    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
  </link>
  <link name="STS3215_elbow_pitch_2_1">
    <inertial>
      <origin rpy="0 0 0" xyz="0.004274566780616719 -0.02198820720088046 -2.525249563345433e-07"/>
      <mass value="0.2843033831904074"/>
      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
    </inertial>
    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
  </link>
  <joint name="elbow_pitch" type="revolute">
    <origin rpy="0 0 0" xyz="0.026719 -0.030548 0.0"/>
    <parent link="STS3215_elbow_pitch_1_1"/>
    <child link="elbow_link_1"/>
    <axis xyz="-0.980528 -0.196381 0.0"/>
    <limit effort="100" lower="-1.570796" upper="1.919862" velocity="100"/>
  </joint>
  <joint name="elbow_wrist_servo_connect" type="fixed">
    <origin rpy="0 0 0" xyz="0.035734 -0.263819 0.002325"/>
    <parent link="elbow_link_1"/>
    <child link="STS3215_wrist_pitch_1"/>
  </joint>
  <joint name="wrist_pitch" type="revolute">
    <origin rpy="0 0 0" xyz="-0.03236 -0.031417 -0.00045"/>
    <parent link="STS3215_wrist_pitch_1"/>
    <child link="wrist_link_1"/>
    <axis xyz="-0.980528 -0.196381 -0.0"/>
    <limit effort="100" lower="-1.919862" upper="1.919862" velocity="100"/>
  </joint>
  <joint name="wrist_wrist_roll_connect" type="fixed">
    <origin rpy="0 0 0" xyz="0.022111 -0.018233 0.0"/>
    <parent link="wrist_link_1"/>
    <child link="STS3215_wrist_roll_1"/>
  </joint>
  <joint name="wrist_roll" type="continuous">
    <origin rpy="0 0 0" xyz="0.009168 -0.037428 0.00045"/>
    <parent link="STS3215_wrist_roll_1"/>
    <child link="gripper_mount_1"/>
    <axis xyz="0.196381 -0.980528 -0.0"/>
  </joint>
  <joint name="wrist_griper_mount_connect" type="fixed">
    <origin rpy="0 0 0" xyz="0.000593 -0.014568 -0.016889"/>
    <parent link="gripper_mount_1"/>
    <child link="STS3215_gripper_1"/>
  </joint>
  <joint name="gripper_moving" type="revolute">
    <origin rpy="0 0 0" xyz="0.019807 0.003967 0.0352"/>
    <parent link="STS3215_gripper_1"/>
    <child link="moving_gripper_1"/>
    <axis xyz="-0.980528 -0.196381 -0.0"/>
    <limit effort="100" lower="-0.20944" upper="1.570796" velocity="100"/>
  </joint>
  <joint name="wrist_mount_connect" type="fixed">
    <origin rpy="0 0 0" xyz="-0.006431 -0.263595 0.002"/>
    <parent link="elbow_link_1"/>
    <child link="wrist_mount_link_1"/>
  </joint>
  <joint name="base_link_mount_connect" type="fixed">
    <origin rpy="0 0 0" xyz="0.0 -0.0554 0.0481"/>
    <parent link="base_link"/>
    <child link="STS3215_base_yaw_1"/>
  </joint>
  <joint name="base_yaw" type="revolute">
    <origin rpy="0 0 0" xyz="0.0 0.0102 -0.0183"/>
    <parent link="STS3215_base_yaw_1"/>
    <child link="base_yaw_link_1"/>
    <axis xyz="0.0 0.0 -1.0"/>
    <limit effort="100" lower="-1.919862" upper="1.919862" velocity="100"/>
  </joint>
  <joint name="base_yaw_link_servo_1_connect" type="fixed">
    <origin rpy="0 0 0" xyz="0.026994 -0.0283 0.0566"/>
    <parent link="base_yaw_link_1"/>
    <child link="STS3215_shoulder_pitch_1_1"/>
  </joint>
  <joint name="base_yaw_link_servo_2_connect" type="fixed">
    <origin rpy="0 0 0" xyz="-0.014013 -0.036513 0.0566"/>
    <parent link="base_yaw_link_1"/>
    <child link="STS3215_shoulder_pitch_2_1"/>
  </joint>
  <joint name="shoulder_pitch" type="revolute">
    <origin rpy="0 0 0" xyz="0.019718 0.004408 0.03475"/>
    <parent link="STS3215_shoulder_pitch_1_1"/>
    <child link="shoulder_link_1"/>
    <axis xyz="0.980528 0.196381 -0.0"/>
    <limit effort="100" lower="-1.745329" upper="1.745329" velocity="100"/>
  </joint>
  <joint name="shoulder_link_servo1_connect" type="fixed">
    <origin rpy="0 0 0" xyz="-0.020553 -0.000547 0.23165"/>
    <parent link="shoulder_link_1"/>
    <child link="STS3215_elbow_pitch_1_1"/>
  </joint>
  <joint name="shoulder_link_servo2_connect" type="fixed">
    <origin rpy="0 0 0" xyz="-0.060875 -0.008622 0.23165"/>
    <parent link="shoulder_link_1"/>
    <child link="STS3215_elbow_pitch_2_1"/>
  </joint>
</robot>

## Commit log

2025-02-16 Add PingTi arm f3d file
2025-02-16 Add 3d print files
    [arm_base_damper_from_so100.stl, arm_base_main_from_so100.stl, arm_base_servo_fmounting_frame_from_so100.stl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]
2025-02-19 Create update arm fusion file and create PyBullet URDF
    [Moving_Jaw_08d1.stl, PingTi_Arm.urdf, STS3215_elbow_lift_11.stl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]
2025-02-20 Rename links and joints based on standard robotics terms
    [PingTi_Arm_5DOF_v1.f3d, base_link_damper_from_so100.stl, base_link_from_so100.stl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]
2025-03-02 Update enhanced base_yaw_link and shoulder_link
    [PingTi_Arm_5DOF_v1.f3d, PingTi_Arm_5DOF_v3.f3d, base_yaw_link.stl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]
2025-03-02 Update README, BOM list, Assembly tutorial and 3d print tutorial
    [wrist_pitch_link_from_so100.stl]
2025-03-02 Update assemble picture
2025-03-04 Update README, BOM list, asembly tutorial
2025-03-06 Update README.md, update lerobot tutorial
    [base_link_idle_clamp_from_so100.stl]
2025-03-20 Enchance shoulder link
    [PingTi_Arm_5DOF_v3.f3d, PingTi_Arm_5DOF_v4.f3d, shoulder_link.stl]
2025-06-30 Update shoulder link stl file
    [shoulder_link.stl]
2025-09-06 Update URDF of PingTi arm
    [Moving_Jaw_08d1.stl, PingTi_Arm.urdf, PingTi_Arm_v3.urdf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]
2025-12-08 added alternate elbow and shoulder links, updated docs
    [elbow_link_alternate.stl, shoulder_link_alternate.stl]
